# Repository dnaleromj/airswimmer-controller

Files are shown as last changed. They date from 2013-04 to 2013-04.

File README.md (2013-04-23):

Airswimmer Controller
======================

Randy wants a fishbowl the size of SPARC.

This PCB is a drop in replacement for the PCB in the device.

Highlights
==========
* Arduino Happy
* 2 brushed motor controllers built in (like in the original circuit)
* 2.4GHZ radio (Phase 2)
* Accellerometer and Gyro built in the so the fish can go where it wants.
* LIPO - 2S right now,  will consider 1S later.

Phase 1
=======

* PCB drawn and sent to the FAB
* Initial Firmware will be made that implements simple autonomous movements
  * Bump into something, move in a different direction
  * Get bored and scoot at random times.
  * 

Phase 2
=======

* Bluetoth/BT Low Enegery on board for iPhone/iPad control
  *  Will support a serial stream command mode
  *  regurgitate onboard stats, battery level,  log of decisions, etc.

Phase 3
=======

* You tell me!

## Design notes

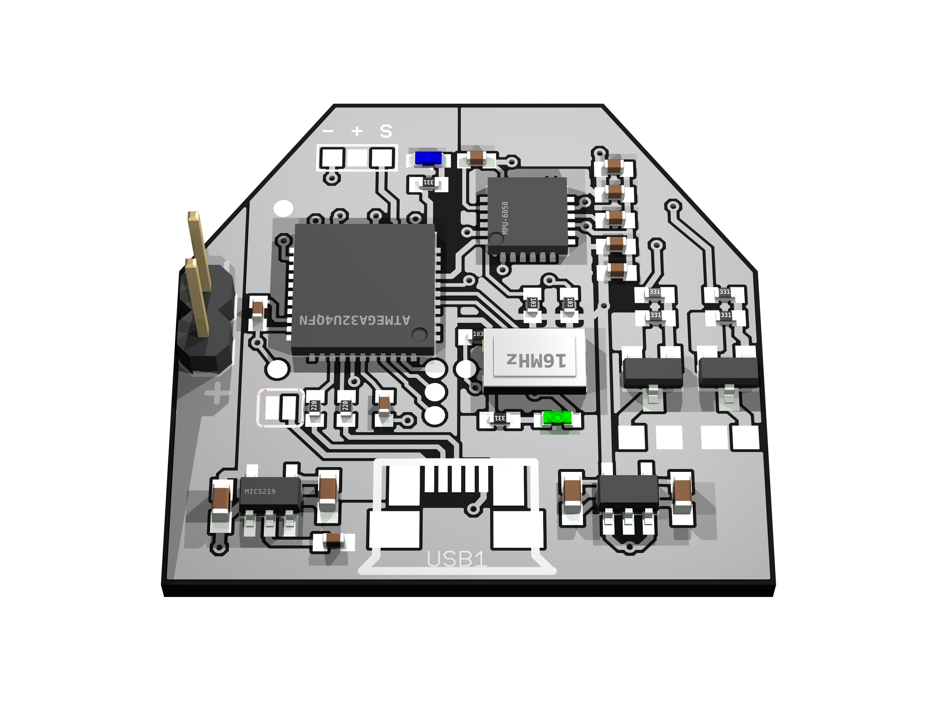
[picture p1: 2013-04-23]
pcb/povray/airswimmer-controller-0-big.png

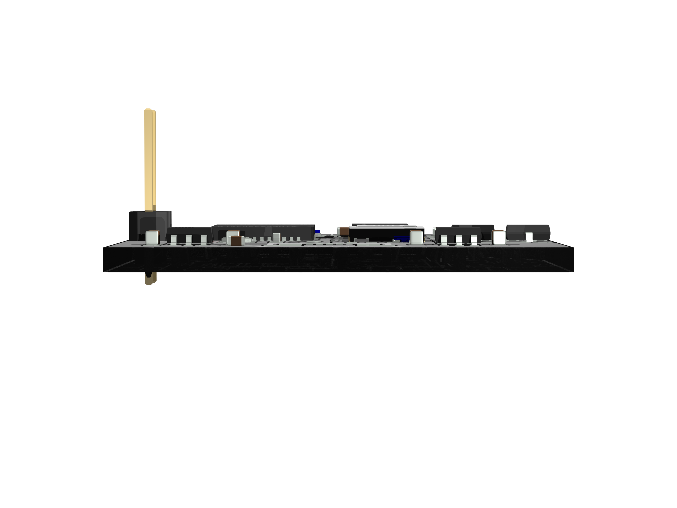
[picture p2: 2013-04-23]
pcb/povray/airswimmer-controller-60-big.png

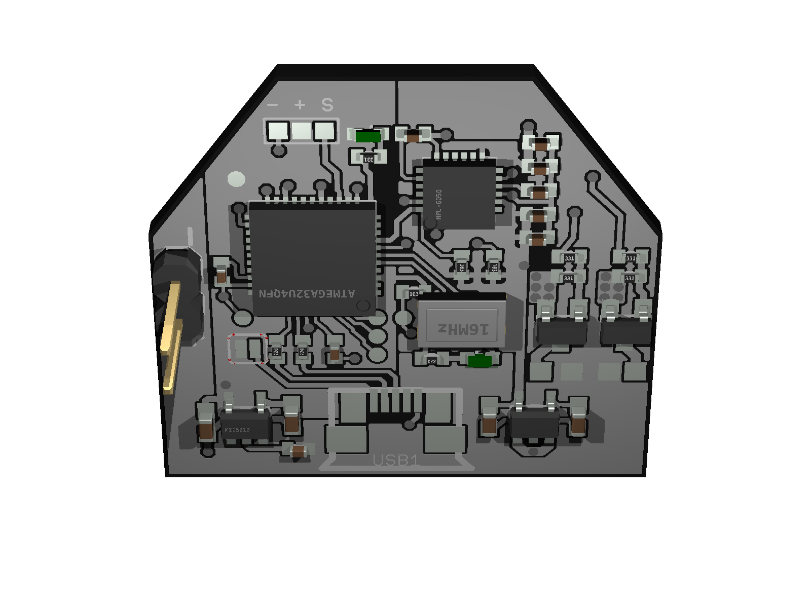
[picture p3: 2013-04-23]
pcb/povray/airswimmer-controller-300.png

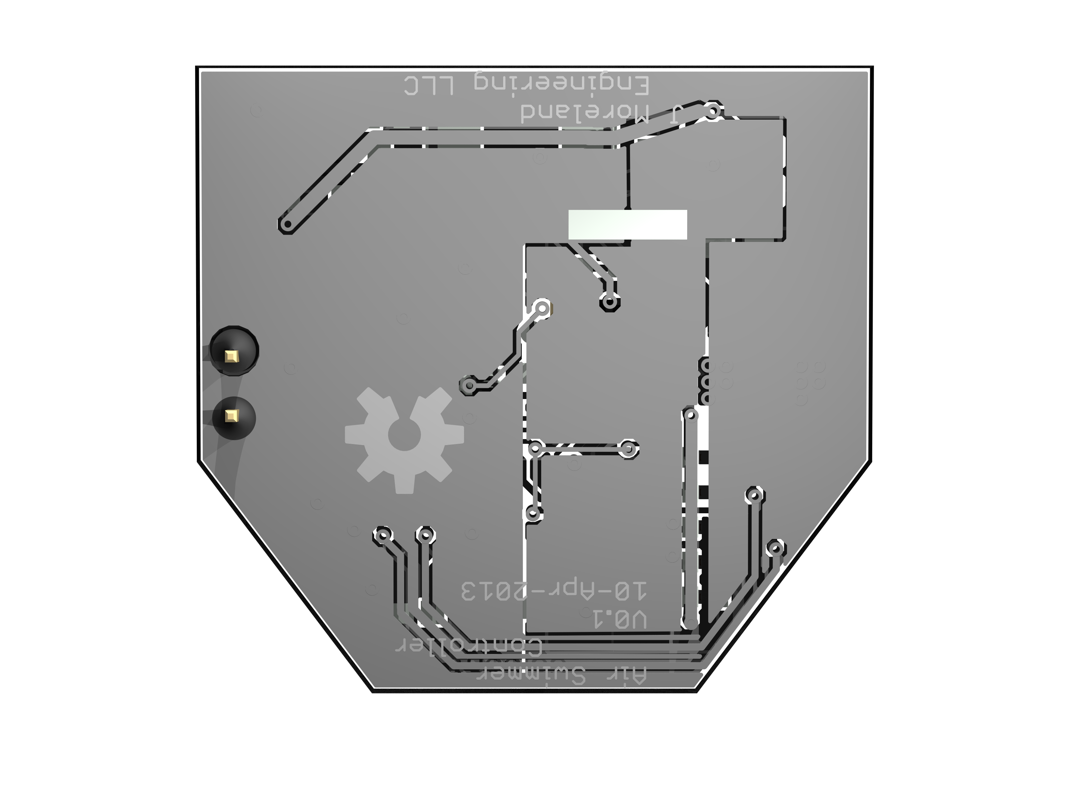
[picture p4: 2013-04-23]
pcb/povray/airswimmer-controller-150-big.png

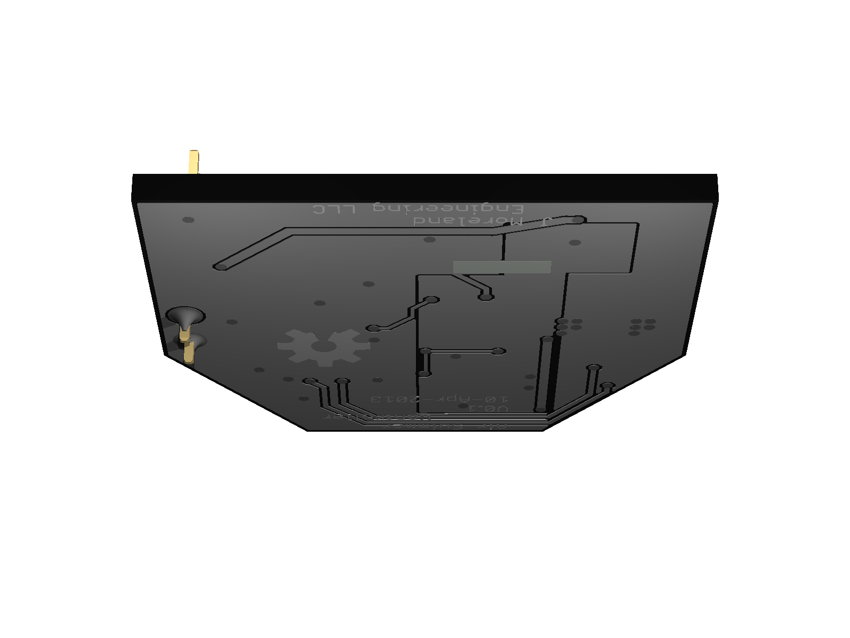
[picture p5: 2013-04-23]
pcb/povray/airswimmer-controller-90.png

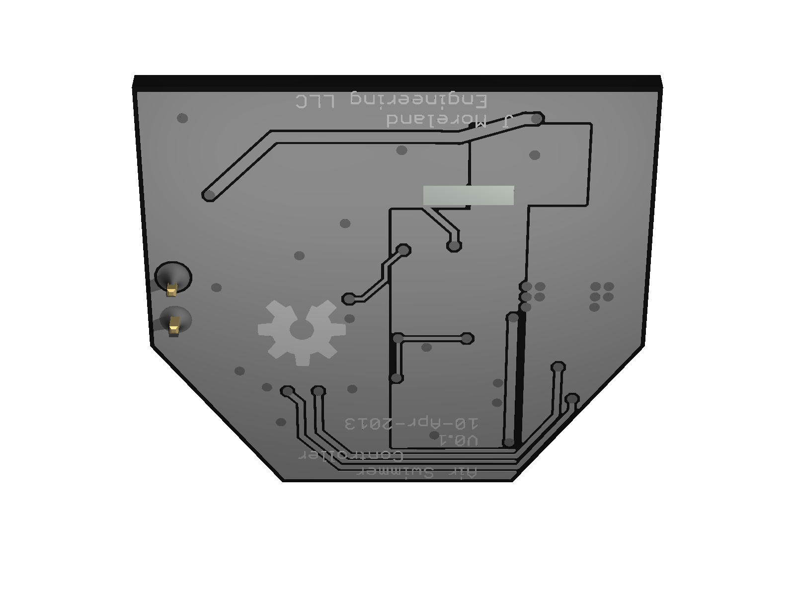
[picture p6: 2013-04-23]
pcb/povray/airswimmer-controller-120.png

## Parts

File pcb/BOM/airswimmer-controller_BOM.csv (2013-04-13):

Qty-1 | Part References | Value | Package | Mfg Part Num | Mfg Name | VID | Vendor Part Num | Description | Pkg Code |  |  |  | XREF
2 | Q1, Q2 |  | SOT23 | DMG6968U-7 | Diodes Inc | DK | DMG6968UDICT-ND | MOSFET N-CH 20V 6.5A SOT-23 | SOT32-3 | * | * | * | REF132
1 | RCIN |  | 3P-SMD-4.1X1.5 | DNP | DO NOT PLACE | (N/A) | DO NOT PLACE | DO NOT PLACE | * | * | * | * | REF14
3 | C9, C11, C13 | 0.1uF | 0402-CAP | GMK105BJ104KV-F | TAIYO YUDEN (VA) | DK | 587-1994-1-ND | CAP CER 0.1UF 35V 10% X5R 0402 | 402 | * | * | * | REF98
2 | C1, C3 | 0.1uF | SPARKFUN_0402-CAP | GMK105BJ104KV-F | TAIYO YUDEN (VA) | DK | 587-1994-1-ND | CAP CER 0.1UF 35V 10% X5R 0402 | 402 | * | * | * | REF98
1 | C2 | 1uF | SPARKFUN_0402-CAP | LMK105BJ105KV-F | TAIYO YUDEN (VA) | DK | 587-1454-1-ND | CAP CER 1UF 10V 10% X5R 0402 | 402 | * | * | * | REF111
1 | C12 | 2.2nF | 0402-CAP | C0402C222K4RACTU | KEMET (VA) | DK | 399-7778-1-ND | CAP CER 2200PF 16V 10% X7R 0402 | 0402 | * | * | * | REF128
3 | R1, R6, R7 | 10k | 0402-RES | CRCW040210K0FKED | VISHAY DALE (VA) | DK | 541-10.0KLCT-ND | RES 10.0K OHM 1/16W 1% 0402 SMD | 402 | * | * | * | REF101
2 | C8, C10 | 10nF | 0402-CAP | C0402C103K8RACTU | KEMET (VA) | DK | 399-7759-1-ND | CAP CER 10000PF 10V 10% X7R 0402 | 0402 | * | * | * | REF127
2 | C4, C5 | 10uF | 0603-CAP | TCM1A106M8R | ROHM SEMICONDUCTOR (PASSIVE) (VA) | DK | 511-1679-1-ND | CAP TANT 10UF 10V 20% 0603 | 603 | * | * | * | REF109
1 | Y1 | 16MHz | RESONATOR-SMD | CSTCE16M0V53-R0 | MURATA ELECTRONICS (VA) | DK | 490-1198-1-ND | CER RESONATOR 16.0MHZ SMD | * | * | * | * | REF107
2 | R4, R5 | 22 | 0402-RES | CRCW040222R0JNED | VISHAY DALE (VA) | DK | 541-22JCT-ND | RES 22 OHM 1/16W 5% 0402 SMD | 402 | * | * | * | REF103
6 | R2, R3, R8, R9, R10, R11 | 330 | 0402-RES | CRCW0402330RJNED | VISHAY DALE (VA) | DK | 541-330JCT-ND | RES 330 OHM 1/16W 5% 0402 SMD | 402 | * | * | * | REF102
2 | C6, C7 | 470pF | 0603-CAP | C0603C471K5RACTU | KEMET (VA) | DK | 399-1075-1-ND | CAP CER 470PF 50V 10% X7R 0603 | 603 | * | * | * | REF119
1 | A32U4 | ATMEGA32U4QFN | ATMEL_QFN-44_SMALL_PAD | ATMEGA32U4-MU | ATMEL | DK | ATMEGA32U4-MU-ND | MCU AVR 32K FLASH 16MHZ 44-QFN | QFN-44 | * | * | * | REF95
1 | LED1 | Blue | LED-0603 | LTST-C191TBKT | LITE-ON INC (VA) | DK | 160-1647-1-ND | LED 468NM BLUE CLEAR 0603 SMD | 603 | * | * | * | REF104
1 | GND_SHORT | GND_SHORT | GND_SHORT | DNP | DO NOT PLACE | (N/A) | DO NOT PLACE | DO NOT PLACE | * | * | * | * | REF14
1 | LED2 | Green | LED-0603 | LTST-C190KGKT | LITE-ON INC (VA) | DK | 160-1435-1-ND | LED GREEN CLEAR 0603 SMD | 603 | * | * | * | REF114
1 | JP6 | LIPO | 1X02_LOCK | DNP | DO NOT PLACE | (N/A) | DO NOT PLACE | DO NOT PLACE | * | * | * | * | REF14
1 | LDO3V3 | MIC5219 3.3V | SOT23-5 | MIC5219-3.3YM5 TR | MICREL INC (VA) | DK | 576-1281-1-ND | IC REG LDO 3.3V .5A SOT23-5 | SOT23-5 | * | * | * | REF129
1 | LDO5V0 | MIC5219 5V | SOT23-5 | MIC5219-5.0YM5 TR | MICREL INC (VA) | DK | 576-2770-1-ND | IC REG LDO 5V .5A SOT23-5 | SOT23-5 | * | * | * | REF105
1 | USB1 | MICRO_USB_B_SMD | MOLEX_MICRO_USB_B_BOTTOM_MOUNT | 473460001 | Molex Inc | DK | WM17141CT-ND | CONN RCPT 5POS MICRO USB R/A | USB MICRO B | * | * | * | REF130
1 | MPU-6050 | MPU-6050 | QFN-24 | ***PART# '*' NOT FOUND*** | * | * | * | * | * | * | * | * | *
1 | LOGO1 | OSHW-LOGOM | OSHW-LOGO-M | DNP | DO NOT PLACE | (N/A) | DO NOT PLACE | DO NOT PLACE | * | * | * | * | REF14
1 | SJ1 | P-USB | SPARKFUN_SJ_2S | DNP | DO NOT PLACE | (N/A) | DO NOT PLACE | DO NOT PLACE | * | * | * | * | REF14
4 | M1+, M1-, M2+, M2- | SOLDER_PAD.05X.05 | SOLDER_PAD_.05X.05 | DNP | DO NOT PLACE | (N/A) | DO NOT PLACE | DO NOT PLACE | * | * | * | * | REF14
6 | GND, MISO, MOSI, RESET, SCK, VCC | TEST_PAD | ICSP_PAD | DNP | DO NOT PLACE | (N/A) | DO NOT PLACE | DO NOT PLACE | * | * | * | * | REF14

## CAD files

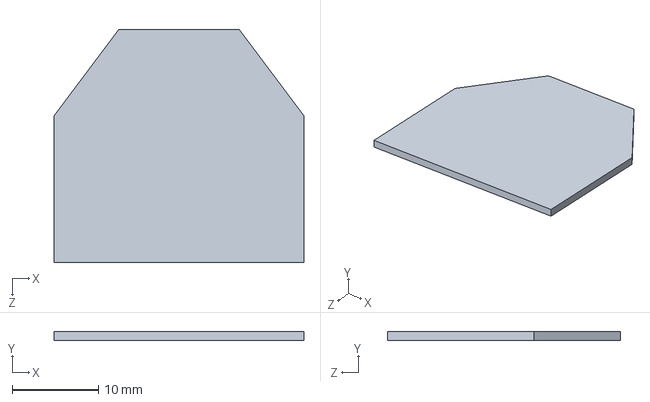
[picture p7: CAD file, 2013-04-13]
drawings/airswimmer-controller.SLDPRT
29.0 x 1.00 x 27.0 mm

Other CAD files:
drawings/airswimmer-controller.DXF

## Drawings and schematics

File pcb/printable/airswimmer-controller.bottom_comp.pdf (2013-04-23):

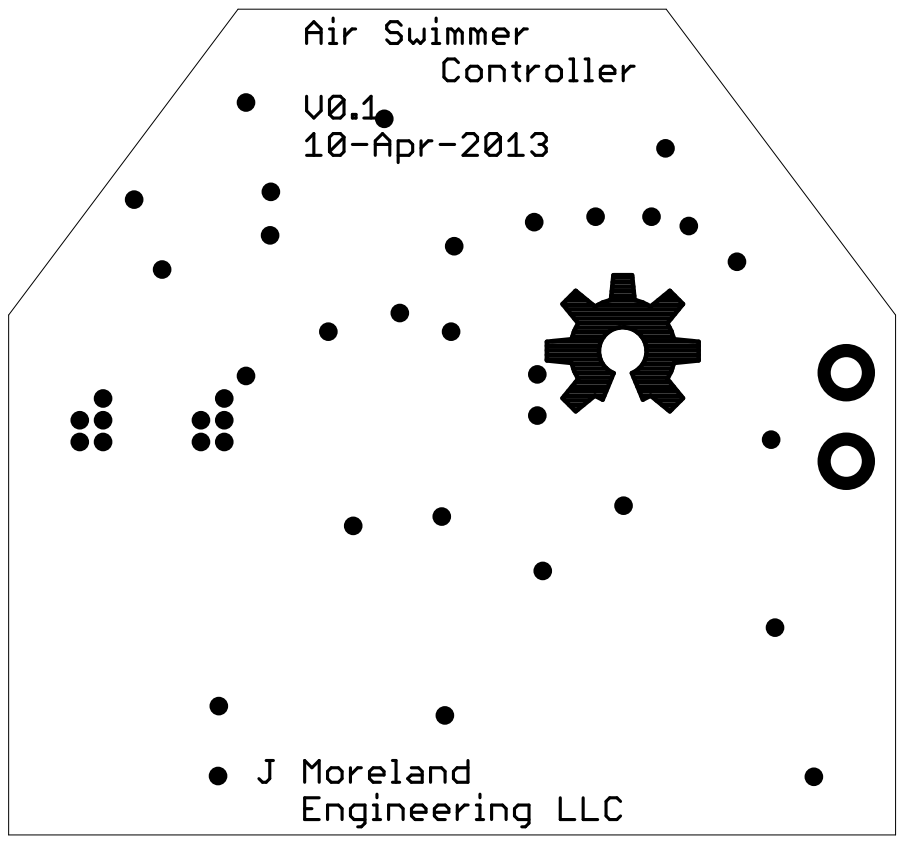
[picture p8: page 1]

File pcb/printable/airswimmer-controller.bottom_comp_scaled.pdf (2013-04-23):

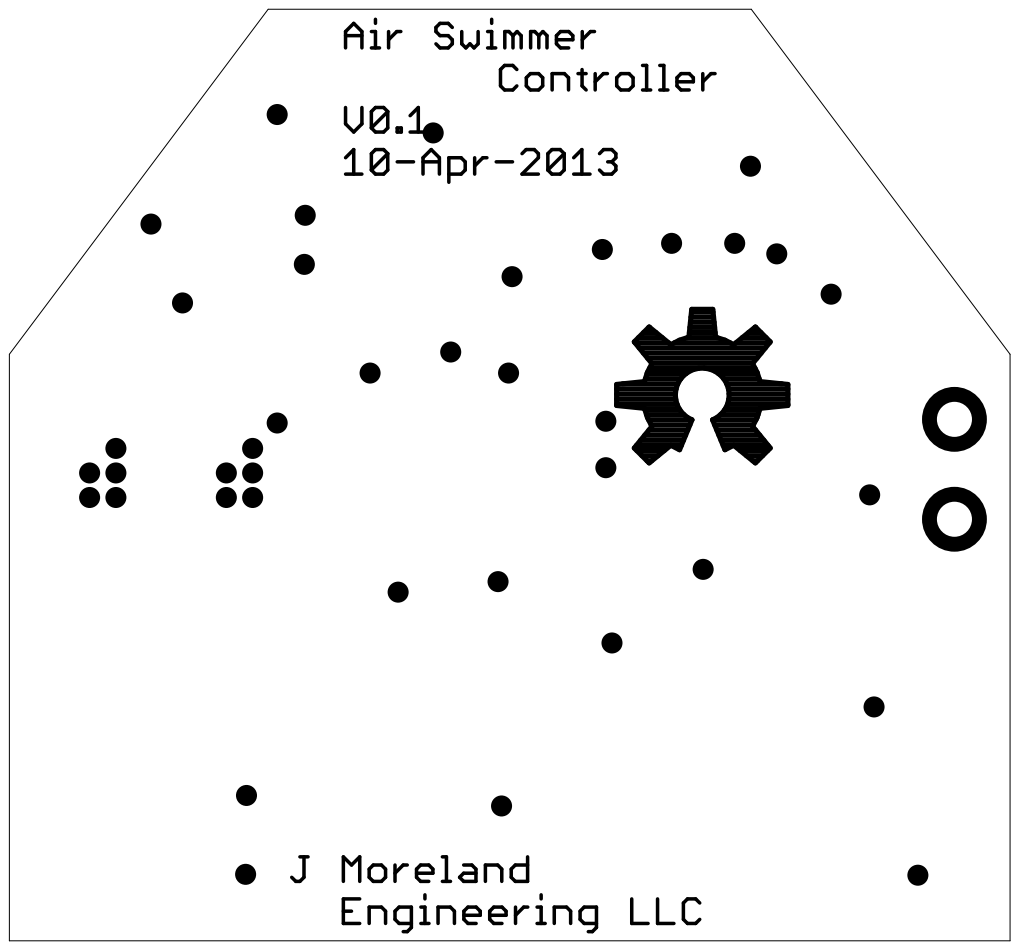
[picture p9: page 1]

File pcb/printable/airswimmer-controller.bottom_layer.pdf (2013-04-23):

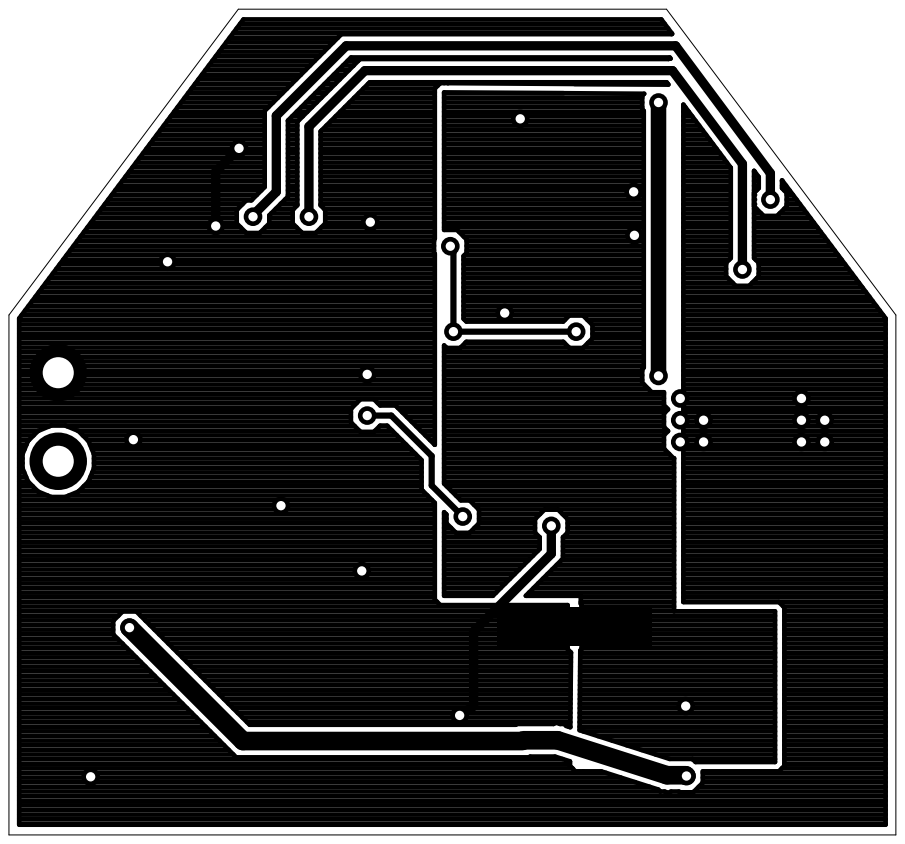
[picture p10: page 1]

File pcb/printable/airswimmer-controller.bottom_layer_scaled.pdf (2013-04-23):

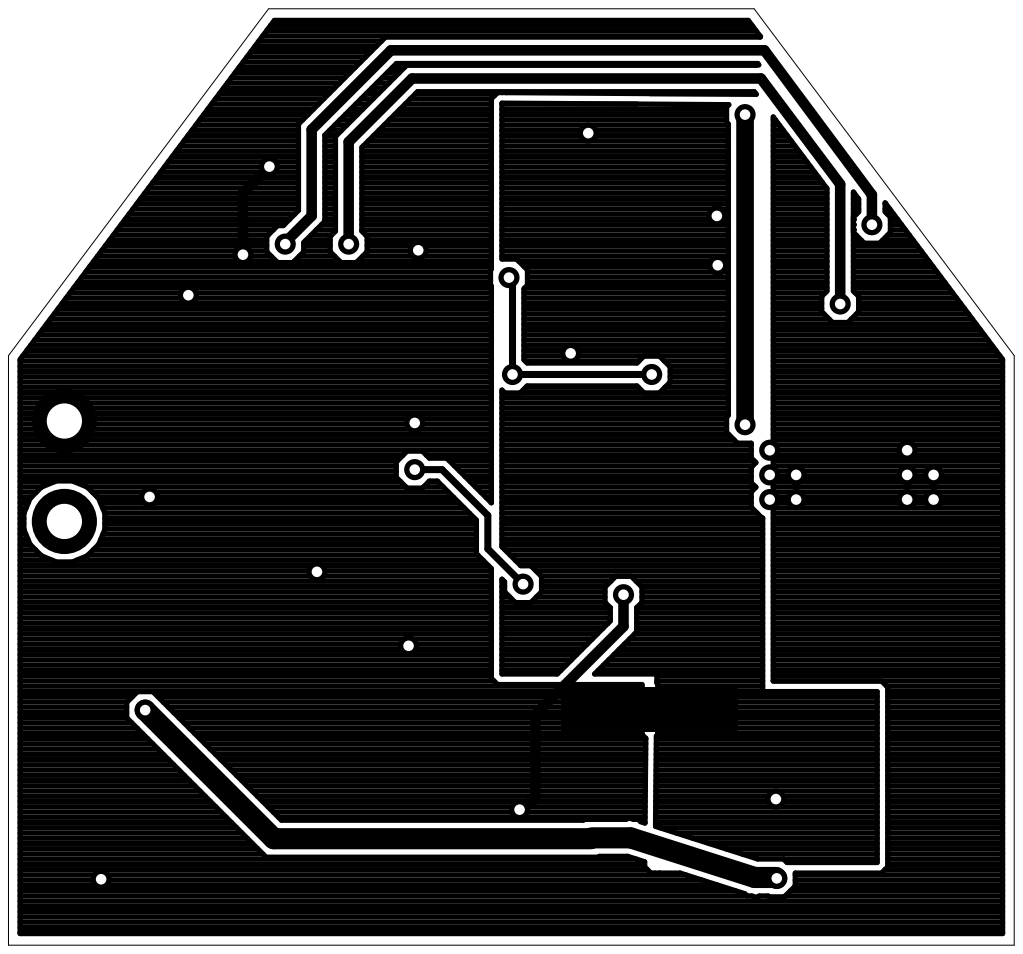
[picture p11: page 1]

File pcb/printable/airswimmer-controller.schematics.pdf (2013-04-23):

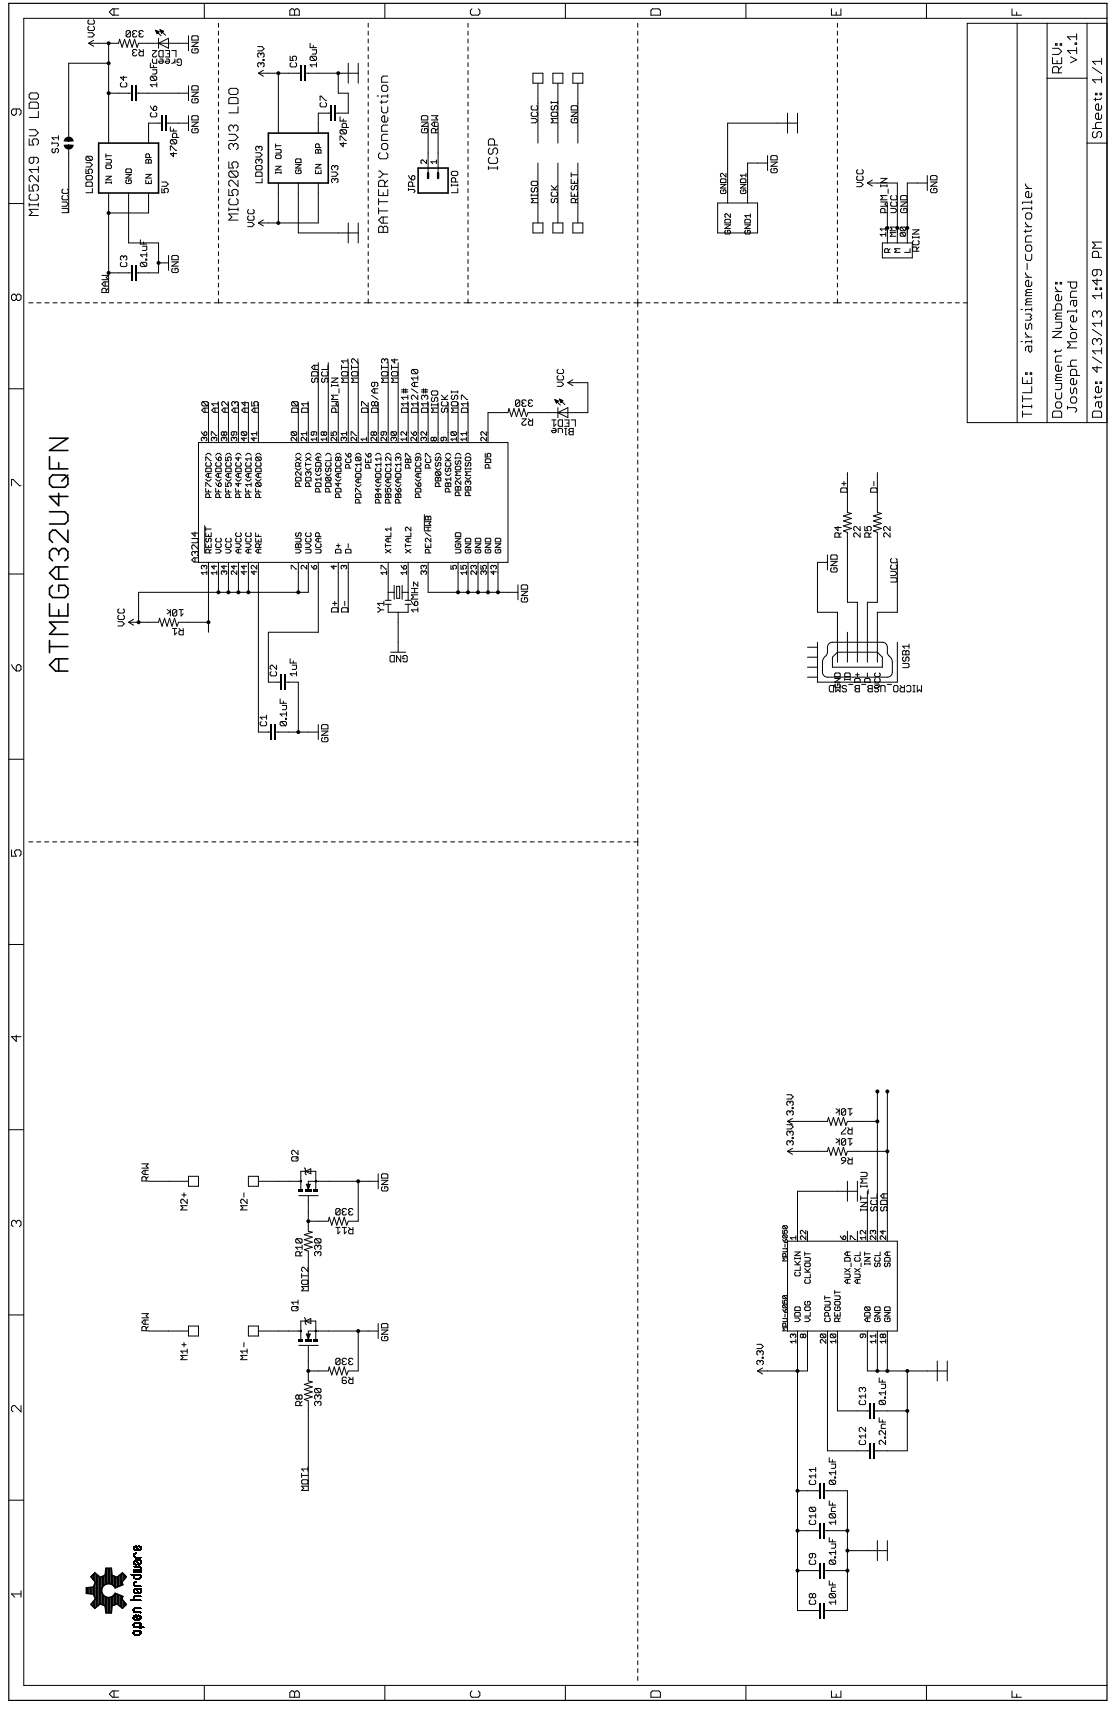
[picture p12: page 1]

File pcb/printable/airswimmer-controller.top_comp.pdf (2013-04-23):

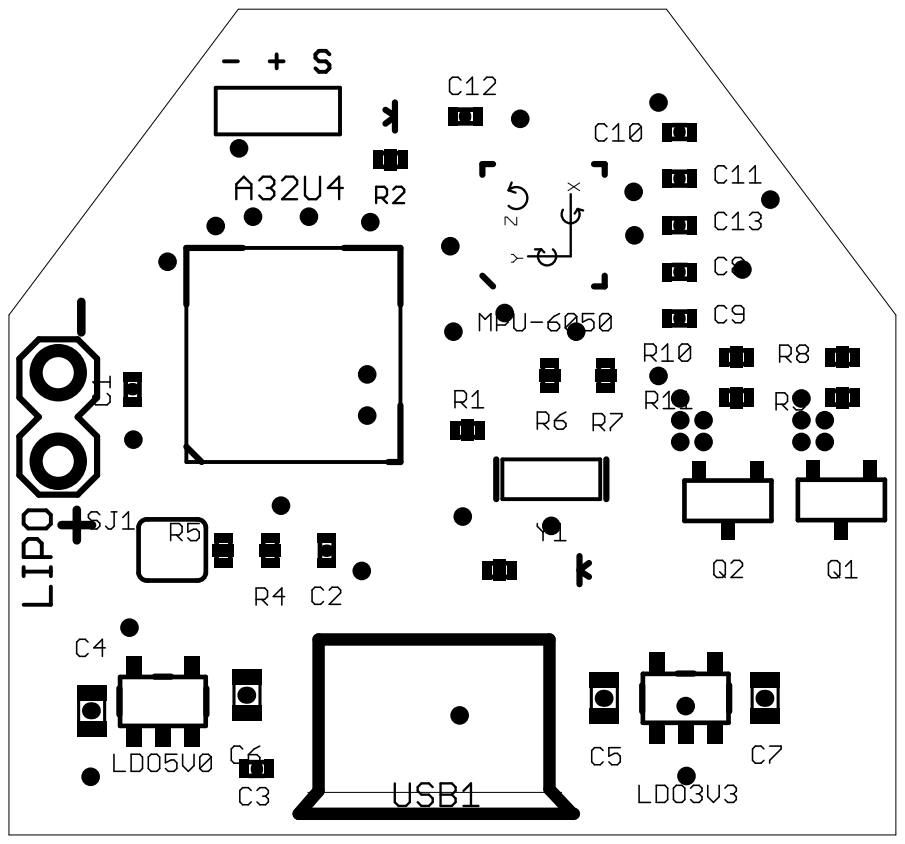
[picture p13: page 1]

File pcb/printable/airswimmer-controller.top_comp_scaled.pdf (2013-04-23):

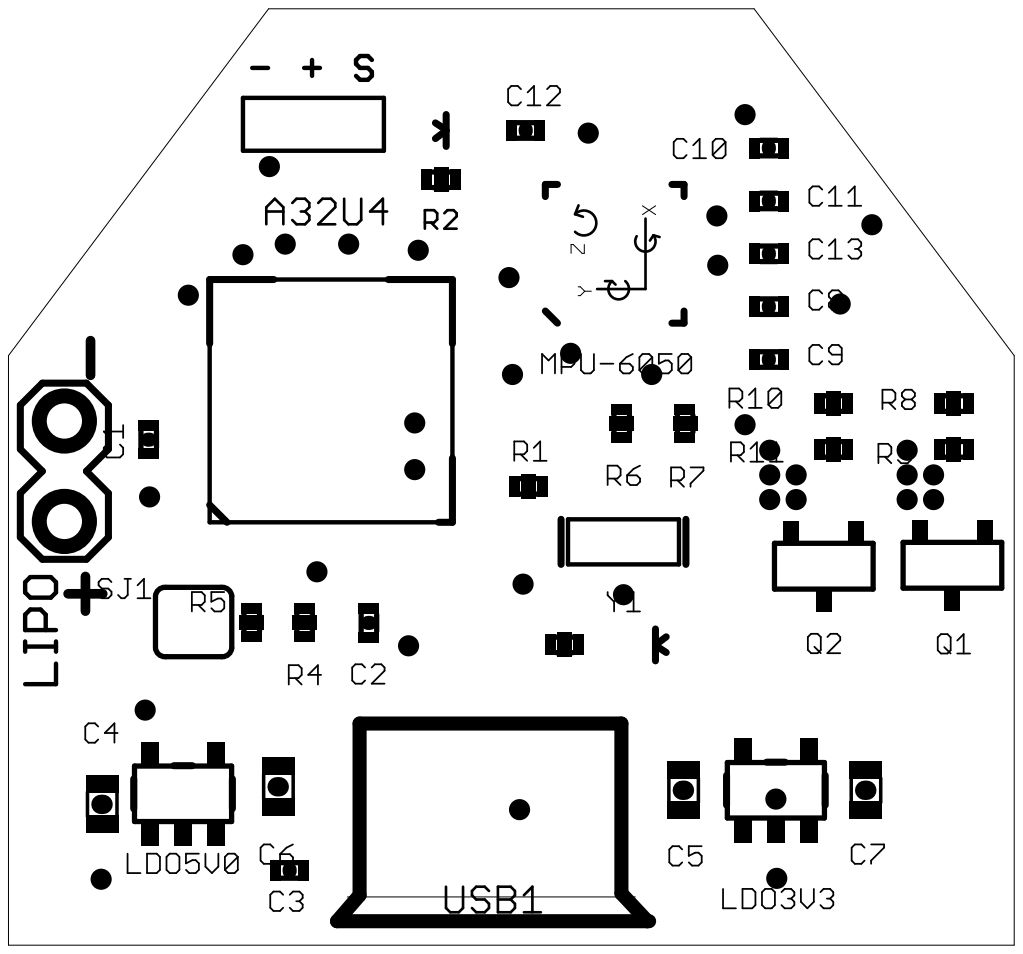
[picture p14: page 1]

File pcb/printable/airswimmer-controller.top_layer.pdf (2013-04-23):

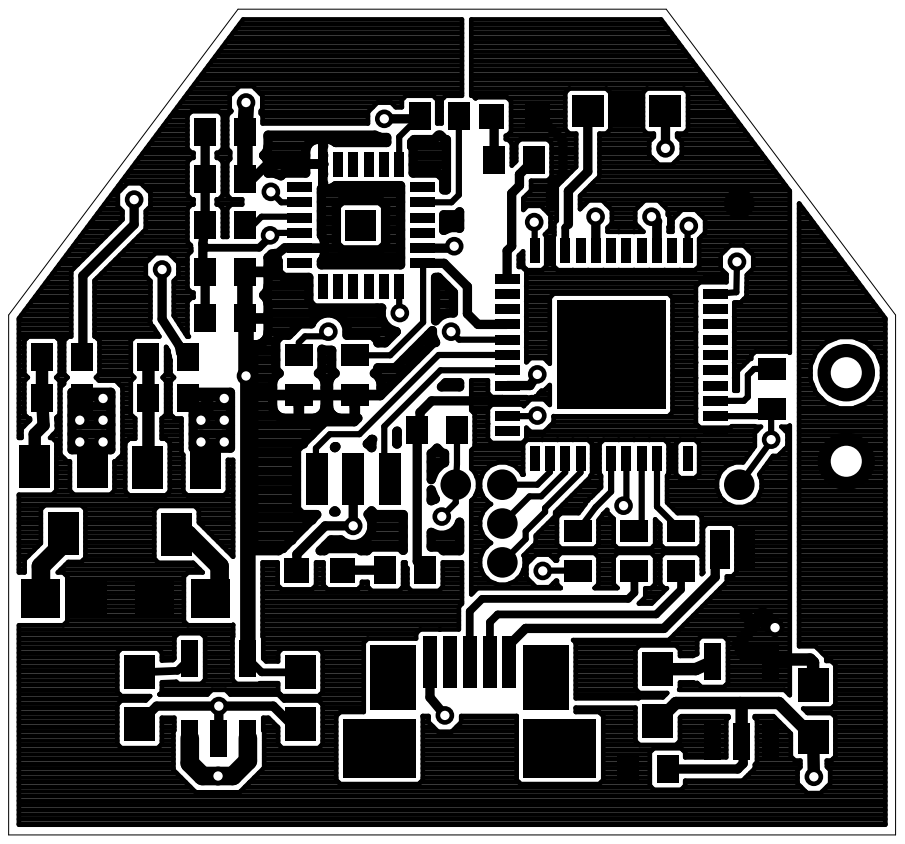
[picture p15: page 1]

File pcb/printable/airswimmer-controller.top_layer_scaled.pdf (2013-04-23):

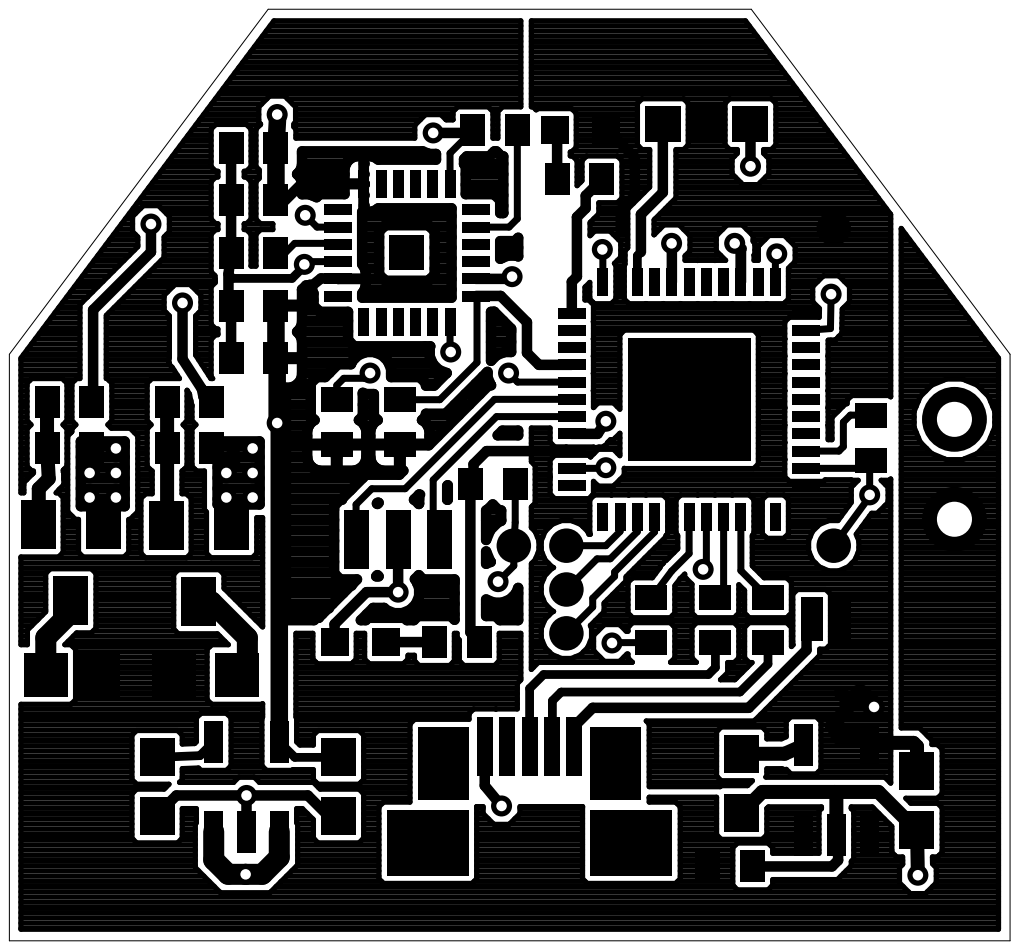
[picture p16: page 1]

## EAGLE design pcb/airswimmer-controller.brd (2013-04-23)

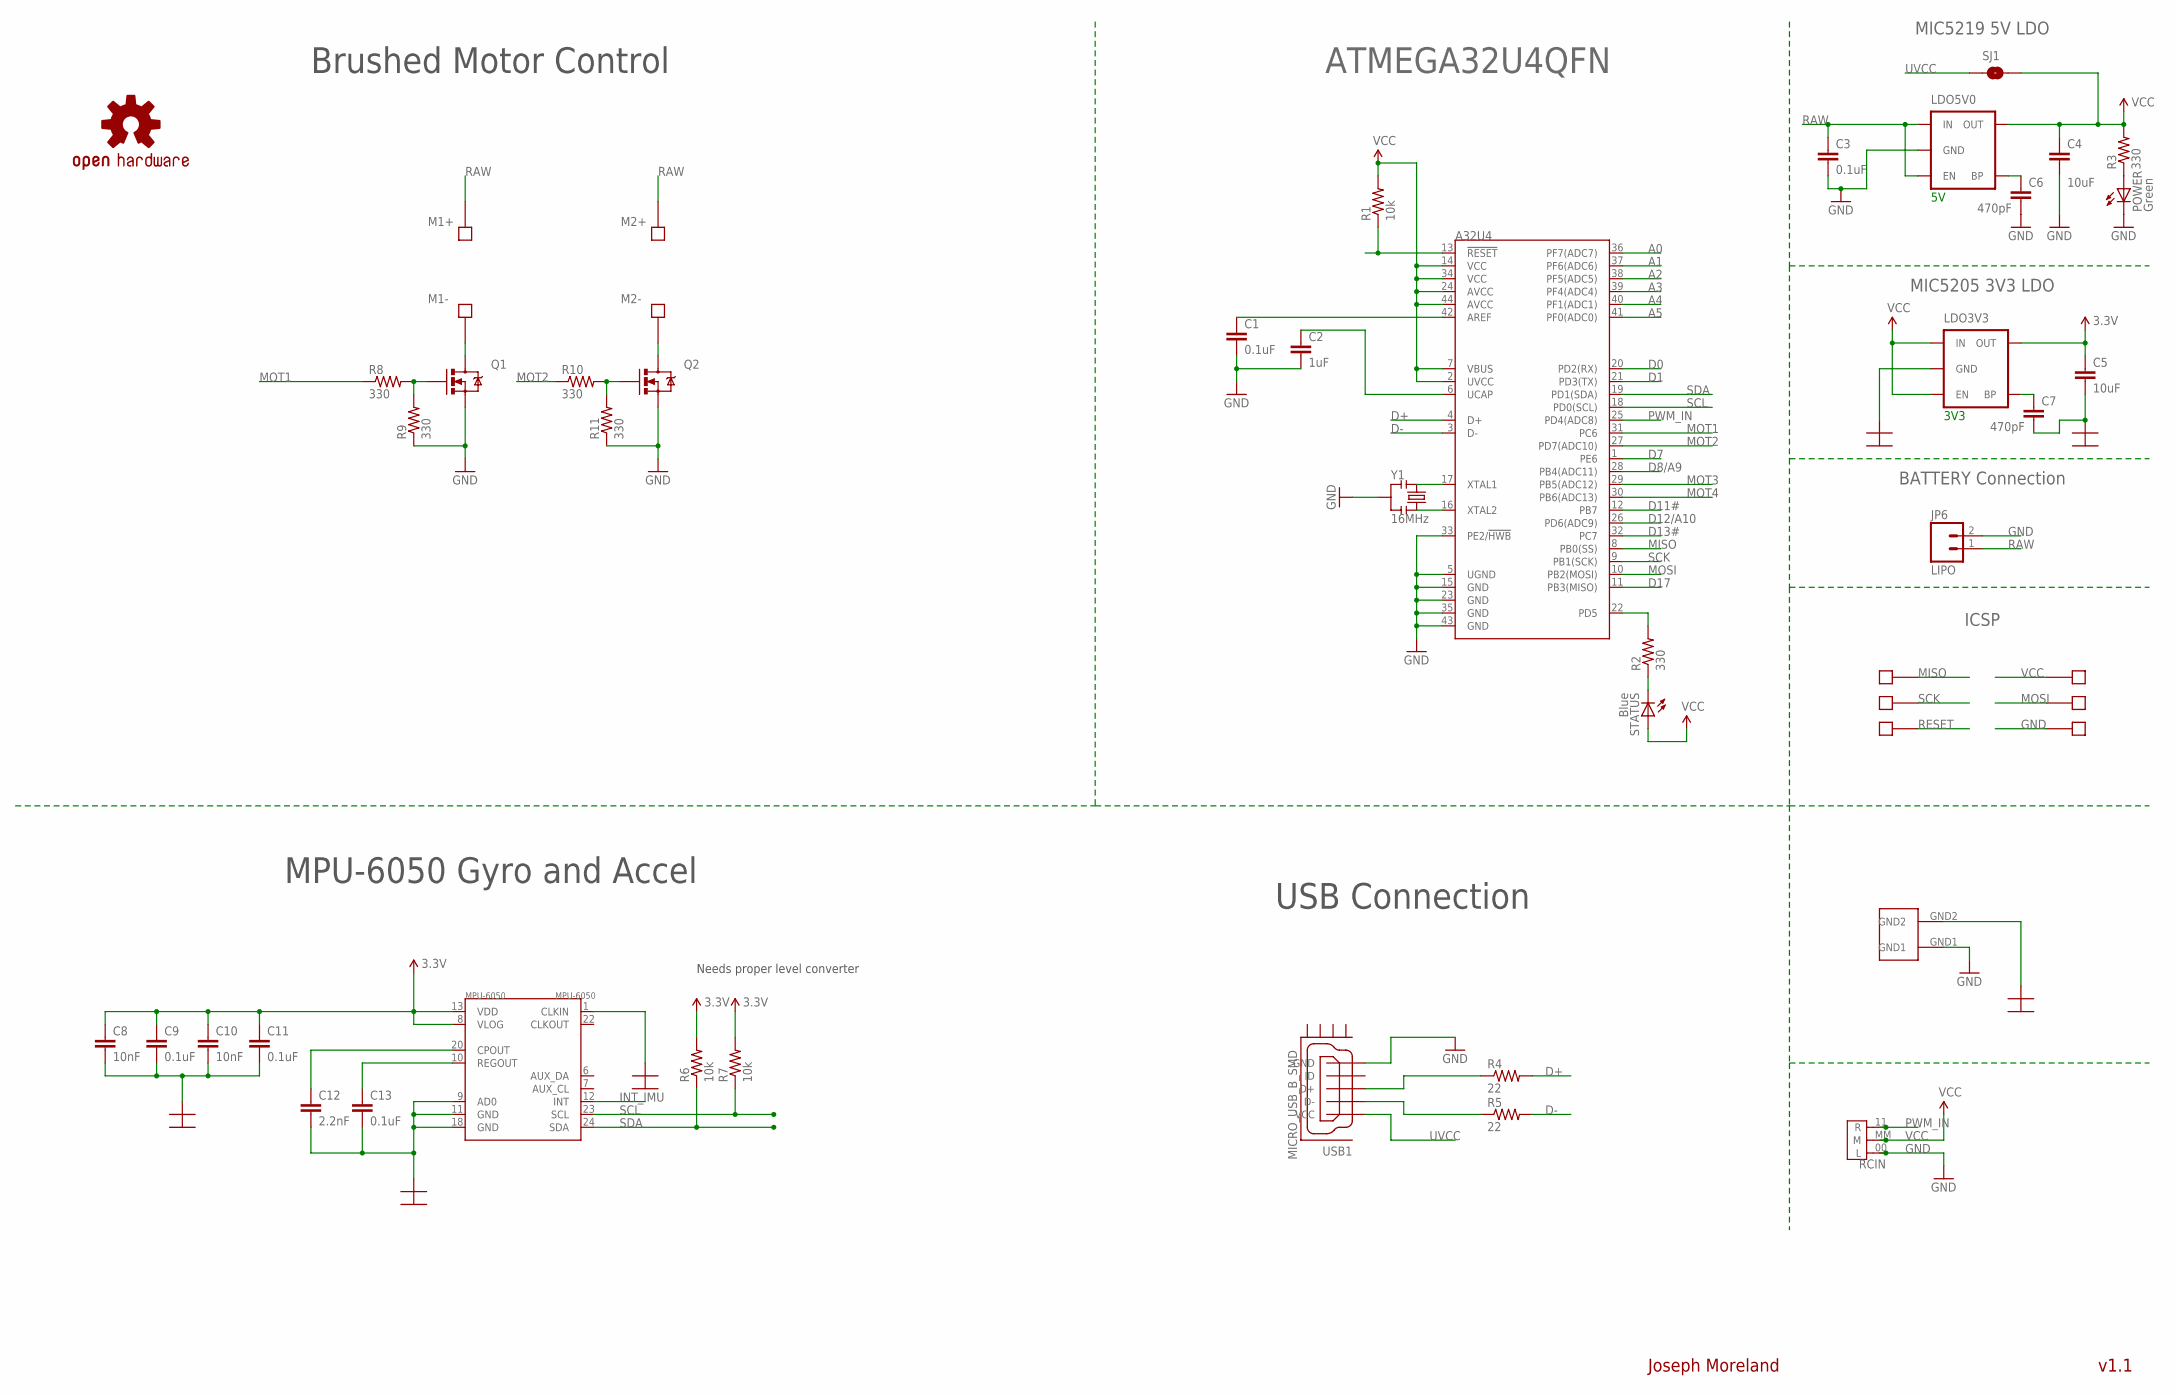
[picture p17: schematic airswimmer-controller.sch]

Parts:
A32U4: ATMEGA32U4QFN; ATMEL_QFN-44_SMALL_PAD; PARTNO ATMEGA32U4-MU
C1, C3: 0.1uF; SPARKFUN_0402-CAP; PARTNO GMK105BJ104KV-F
C2: 1uF; SPARKFUN_0402-CAP; PARTNO LMK105BJ105KV-F
C4, C5: 10uF; 0603-CAP; PARTNO TCM1A106M8R
C6, C7: 470pF; 0603-CAP; PARTNO C0603C471K5RACTU
C8, C10: 10nF; 0402-CAP; PARTNO C0402C103K8RACTU
C9, C11, C13: 0.1uF; 0402-CAP; PARTNO GMK105BJ104KV-F
C12: 2.2nF; 0402-CAP; PARTNO C0402C222K4RACTU
GND: TEST_PAD; ICSP_PAD; PARTNO DNP
GND_SHORT: GND_SHORT; PARTNO DNP
JP6: LIPO; 1X02_LOCK; PARTNO DNP
LDO3V3: V_REG_MIC52193.3V; SOT23-5; PARTNO MIC5219-3.3YM5 TR
LDO5V0: MIC5219; SOT23-5; PARTNO MIC5219-5.0YM5 TR
LOGO1: OSHW-LOGOM; OSHW-LOGO-M; PARTNO DNP
M1+, M1-, M2+, M2-: SOLDER_PAD.05X.05; SOLDER_PAD_.05X.05; PARTNO DNP
MISO: TEST_PAD; ICSP_PAD; PARTNO DNP
MOSI: TEST_PAD; ICSP_PAD; PARTNO DNP
MPU-6050: MPU-6050; QFN-24; PARTNO *
POWER: Green; LED-0603; PARTNO LTST-C190KGKT
Q1, Q2: MOSFET-NCHANNELBSS123LT1G; SOT23; PARTNO DMG6968U-7
R1, R6, R7: 10k; 0402-RES; PARTNO CRCW040210K0FKED
R2, R3, R8, R9, R10, R11: 330; 0402-RES; PARTNO CRCW0402330RJNED
R4, R5: 22; 0402-RES; PARTNO CRCW040222R0JNED
RCIN: PAD-JUMPER-3P40*40; 3P-SMD-4.1X1.5; PARTNO DNP
RESET: TEST_PAD; ICSP_PAD; PARTNO DNP
SCK: TEST_PAD; ICSP_PAD; PARTNO DNP
SJ1: P-USB; SPARKFUN_SJ_2S; PARTNO DNP
STATUS: Blue; LED-0603; PARTNO LTST-C191TBKT
USB1: MICRO_USB_B_SMD; MOLEX_MICRO_USB_B_BOTTOM_MOUNT; PARTNO 473460001
VCC: TEST_PAD; ICSP_PAD; PARTNO DNP
Y1: 16MHz; RESONATOR-SMD; PARTNO CSTCE16M0V53-R0

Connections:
3.3V: C5.1, C8.1, C9.1, C10.1, C11.1, LDO3V3.5 (OUT), MPU-6050.8 (VLOG), MPU-6050.13 (VDD), R6.2, R7.2
A0: A32U4.36 (PF7(ADC7))
A1: A32U4.37 (PF6(ADC6))
A2: A32U4.38 (PF5(ADC5))
A3: A32U4.39 (PF4(ADC4))
A4: A32U4.40 (PF1(ADC1))
A5: A32U4.41 (PF0(ADC0))
AREF: A32U4.42 (AREF), C1.1
D0: A32U4.20 (PD2(RX))
D1: A32U4.21 (PD3(TX))
D7: A32U4.1 (PE6)
D8/A9: A32U4.28 (PB4(ADC11))
D11#: A32U4.12 (PB7)
D12/A10: A32U4.26 (PD6(ADC9))
D13#: A32U4.32 (PC7)
D17: A32U4.11 (PB3(MISO))
D+: A32U4.4 (D+), R4.2
D-: A32U4.3 (D-), R5.2
DGND: C5.2, C7.2, C8.2, C9.2, C10.2, C11.2, C12.2, C13.2, GND_SHORT.GND2, LDO3V3.2 (GND), MPU-6050.1 (CLKIN), MPU-6050.9 (AD0), MPU-6050.11 (GND), MPU-6050.18 (GND)
GND: A32U4.5 (UGND), A32U4.15 (GND), A32U4.23 (GND), A32U4.33 (PE2/!HWB), A32U4.35 (GND), A32U4.43 (GND), C1.2, C2.2, C3.2, C4.2, C6.2, GND.P$1, GND_SHORT.GND1, JP6.2, LDO5V0.2 (GND), POWER.C, Q1.2 (S), Q2.2 (S), R9.1, R11.1, RCIN.00 (L), USB1.5 (GND), Y1.2
INT_IMU: MPU-6050.12 (INT)
MISO: A32U4.8 (PB0(SS)), MISO.P$1
MOSI: A32U4.10 (PB2(MOSI)), MOSI.P$1
MOT1: A32U4.31 (PC6), R8.1
MOT2: A32U4.27 (PD7(ADC10)), R10.1
MOT3: A32U4.29 (PB5(ADC12))
MOT4: A32U4.30 (PB6(ADC13))
unnamed: R4.1, USB1.3 (D+)
unnamed: C6.1, LDO5V0.4 (BP)
unnamed: A32U4.17 (XTAL1), Y1.1
unnamed: C7.1, LDO3V3.4 (BP)
unnamed: M1-.P$1, Q1.3 (D)
unnamed: A32U4.16 (XTAL2), Y1.3
unnamed: R2.1, STATUS.C
unnamed: M2-.P$1, Q2.3 (D)
unnamed: POWER.A, R3.1
unnamed: R5.1, USB1.2 (D-)
unnamed: C13.1, MPU-6050.10 (REGOUT)
unnamed: C12.1, MPU-6050.20 (CPOUT)
unnamed: Q1.1 (G), R8.2, R9.2
unnamed: Q2.1 (G), R10.2, R11.2
unnamed: A32U4.22 (PD5), R2.2
PWM_IN: A32U4.25 (PD4(ADC8)), RCIN.11 (R)
RAW: C3.1, JP6.1, LDO5V0.1 (IN), LDO5V0.3 (EN), M1+.P$1, M2+.P$1
RESET: A32U4.13 (!RESET), R1.1, RESET.P$1
SCK: A32U4.9 (PB1(SCK)), SCK.P$1
SCL: A32U4.18 (PD0(SCL)), MPU-6050.23 (SCL), R7.1
SDA: A32U4.19 (PD1(SDA)), MPU-6050.24 (SDA), R6.1
UCAP: A32U4.6 (UCAP), C2.1
UVCC: SJ1.1, USB1.1 (VCC)
VCC: A32U4.2 (UVCC), A32U4.7 (VBUS), A32U4.14 (VCC), A32U4.24 (AVCC), A32U4.34 (VCC), A32U4.44 (AVCC), C4.1, LDO3V3.1 (IN), LDO3V3.3 (EN), LDO5V0.5 (OUT), R1.2, R3.2, RCIN.MM (M), SJ1.2, STATUS.A, VCC.P$1

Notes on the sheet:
3V3
MIC5219 5V LDO
MIC5205 3V3 LDO
BATTERY Connection
Joseph Moreland
v1.1
Brushed Motor Control
Needs proper level converter
ICSP
USB Connection
MPU-6050 Gyro and Accel

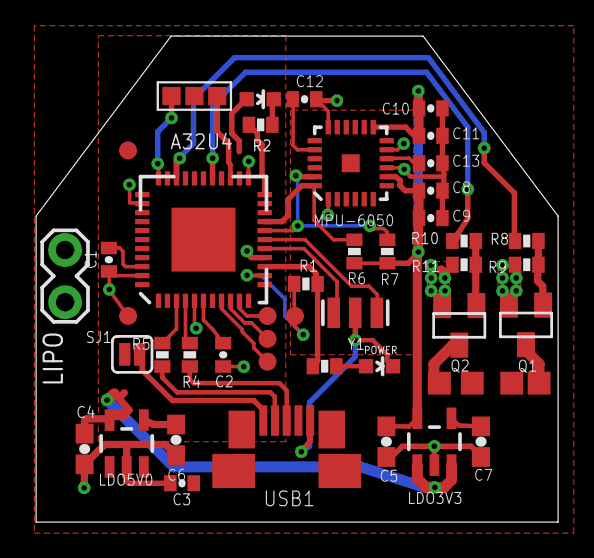
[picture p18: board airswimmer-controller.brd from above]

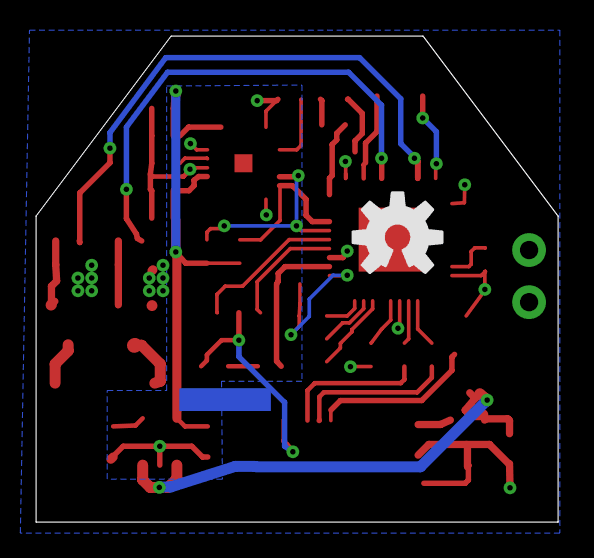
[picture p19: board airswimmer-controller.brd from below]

Board: 2 copper layers, 29.0 x 27.0 mm, 49 parts (2 on the bottom side), 34 nets.

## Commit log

2013-04-13 Initial repo
    [airswimmer-controller.DXF, airswimmer-controller.SLDPRT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]
2013-04-23 Reorg to the standard JCM layout.
    [airswimmer-controller.DXF, airswimmer-controller.SLDPRT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]
2013-04-23 Correct LED cathode direction in schematic.
2013-04-23 Correct LED cathode direction in schematic and board.
    [airswimmer-controller.brd, airswimmer-controller.sch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]
2013-04-23 Added Solidworks board drawing.
    [airswimmer-controller.SLDPRT]

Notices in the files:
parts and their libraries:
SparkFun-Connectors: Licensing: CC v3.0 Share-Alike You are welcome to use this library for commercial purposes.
